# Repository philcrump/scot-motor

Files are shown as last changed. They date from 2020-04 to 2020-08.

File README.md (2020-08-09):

# scot-motor

Motor Interface for the SCOT.

* 9-36V DC Input
* STM32F042K6 Microcontroller @ 48MHz
* MCP2562 CAN 2.0A/B Communication Interface
* DRV8872 3.6A PWM H-Bridge Motor Driver
* INA260 Motor Voltage & Current Supply Monitoring
* NCV8450 800mA Clutch Driver
* E-Stop, End-of-travel Limit Interlocks support
  * Hardware CMOS NAND Logic (immune to software override)
  * Opto-isolation of Switches from Logic Inputs (power supply not isolated)

[**Circuit Board Schematic**](https://github.com/philcrump/scot-motor/raw/master/scot-motor-schematic.pdf)

## PCB (CAD Render)

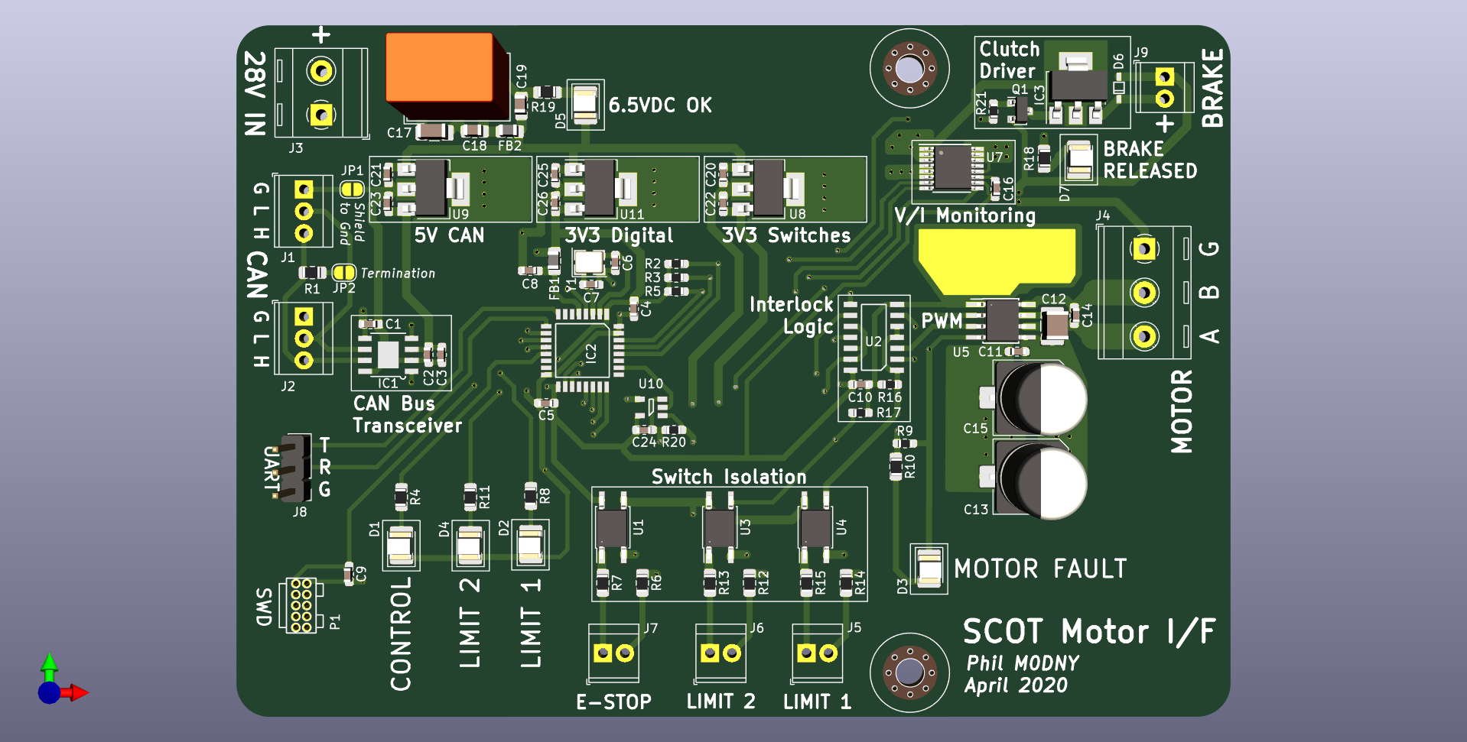
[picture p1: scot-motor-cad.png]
PCB CAD Render


### Errata - April 2020

* ~~0603 footprint used for C3 (4.7uF, 25V), should be 0805 - Minimal impact, 0805 still fits.~~ - Fixed in August 2020.

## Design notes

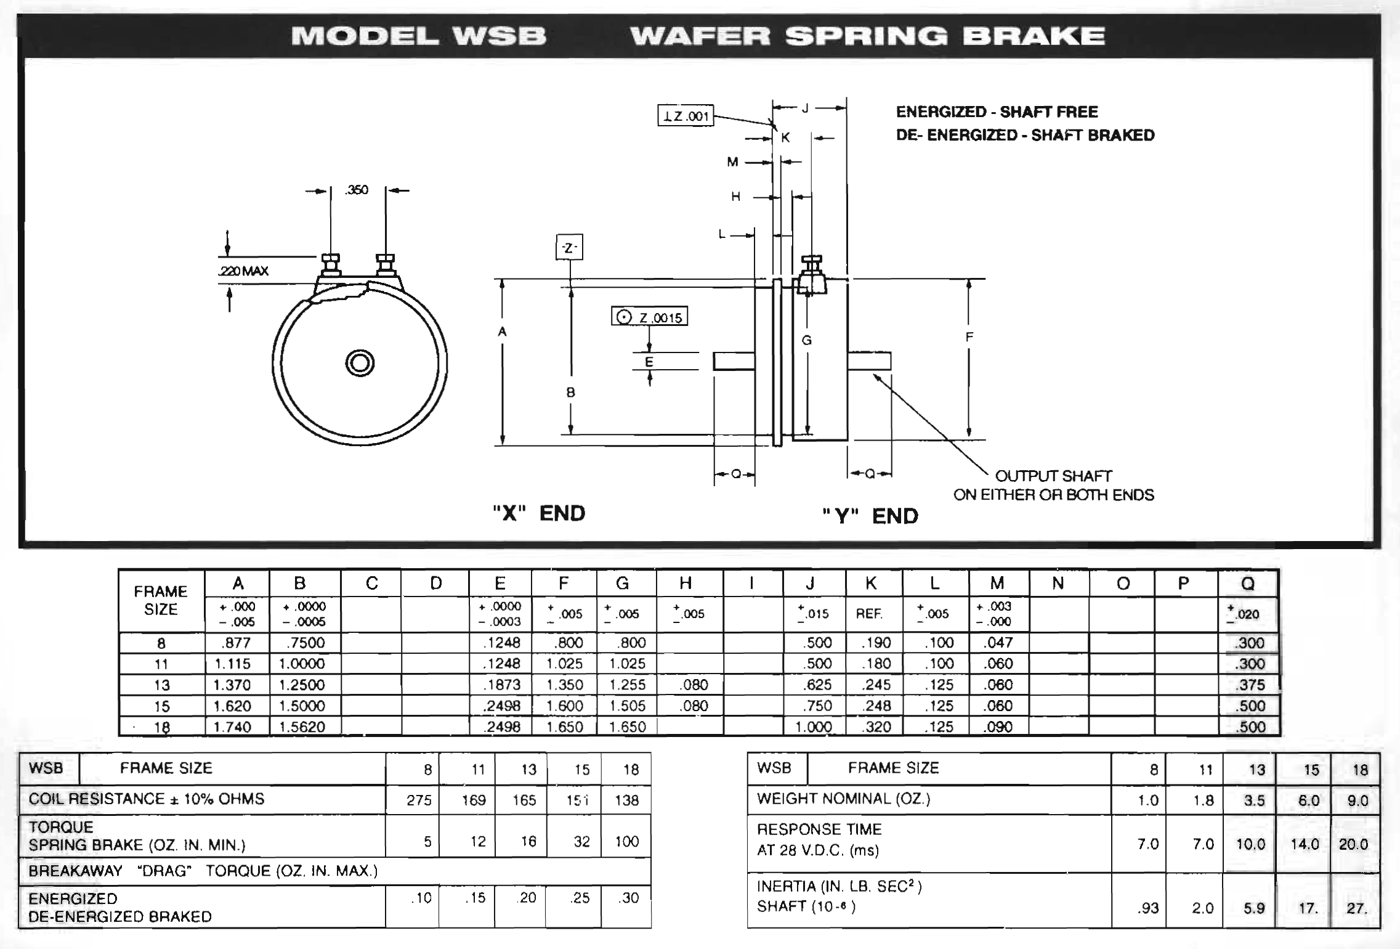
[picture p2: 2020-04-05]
datasheets/WSB_Brake.png

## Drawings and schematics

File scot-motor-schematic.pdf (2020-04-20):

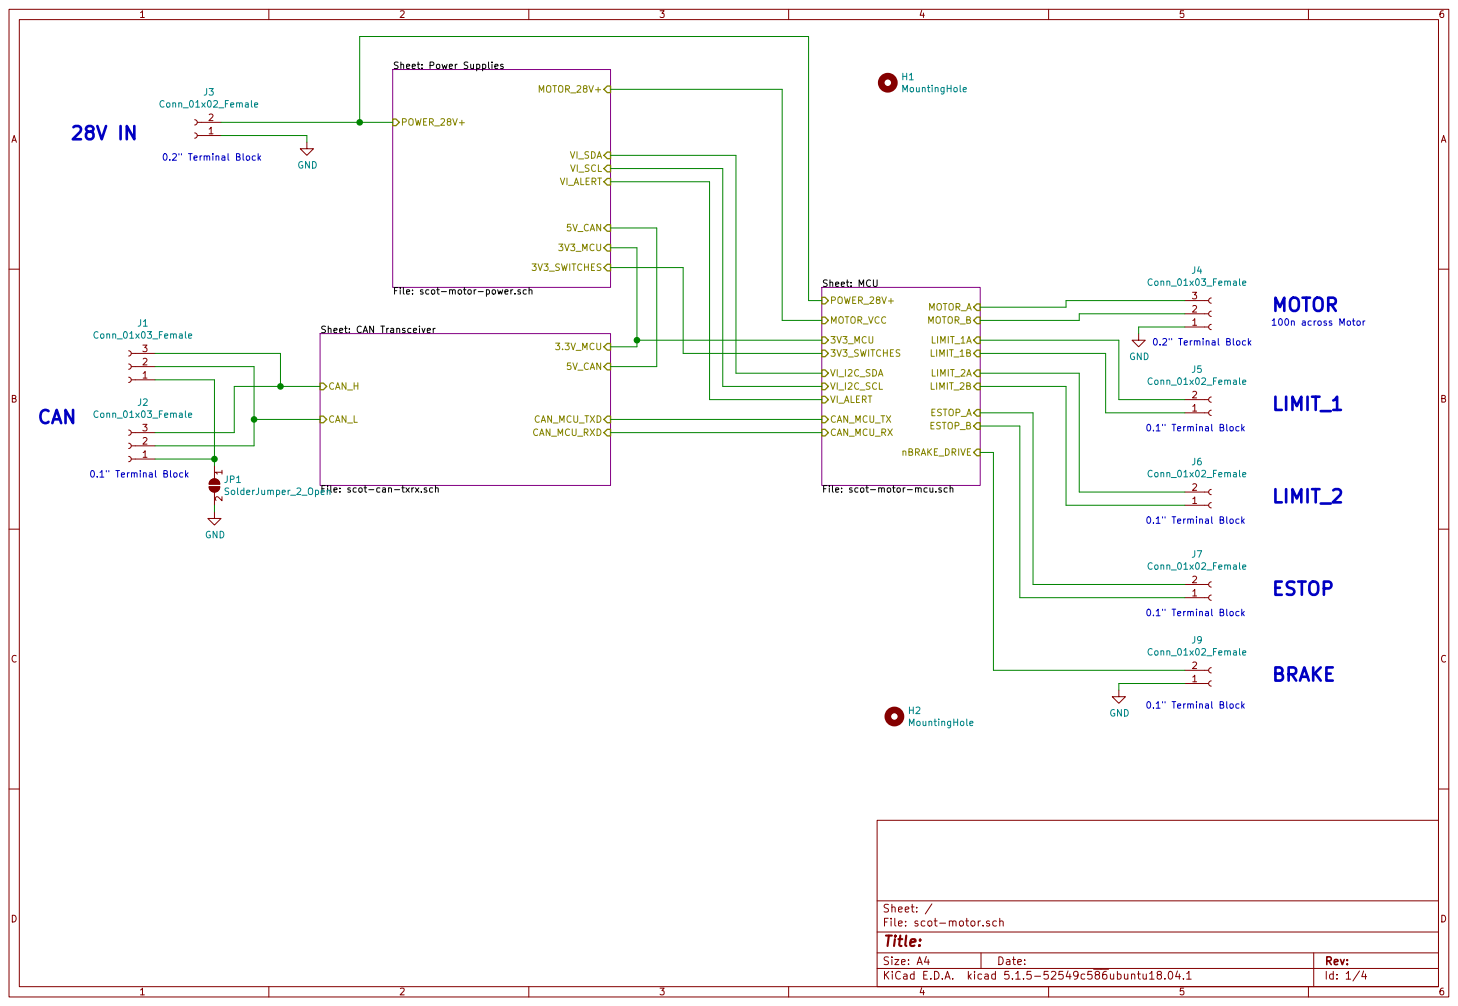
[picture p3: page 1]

File: scot-motor-power.sch POWER_28V+

Sheet: CAN Transceiver File: scot-can-txrx.sch CAN_L CAN_H

0.2" Terminal Block 0.1" Terminal Block 0.1" Terminal Block 0.1" Terminal Block CAN

Id: 1/4 Title: File: scot-motor.sch Sheet: /

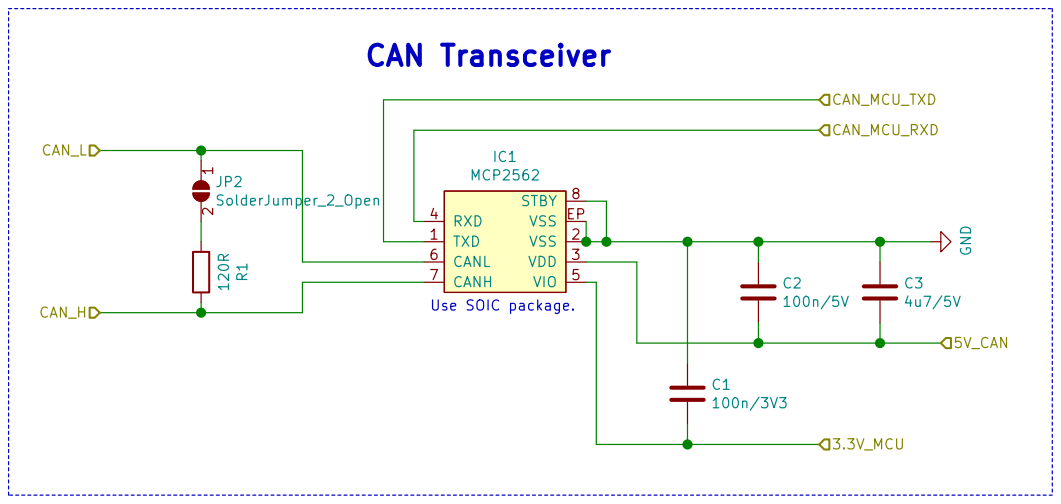
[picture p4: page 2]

Id: 2/4 Title: File: scot-can-txrx.sch Sheet: /CAN Transceiver/ R1 120R

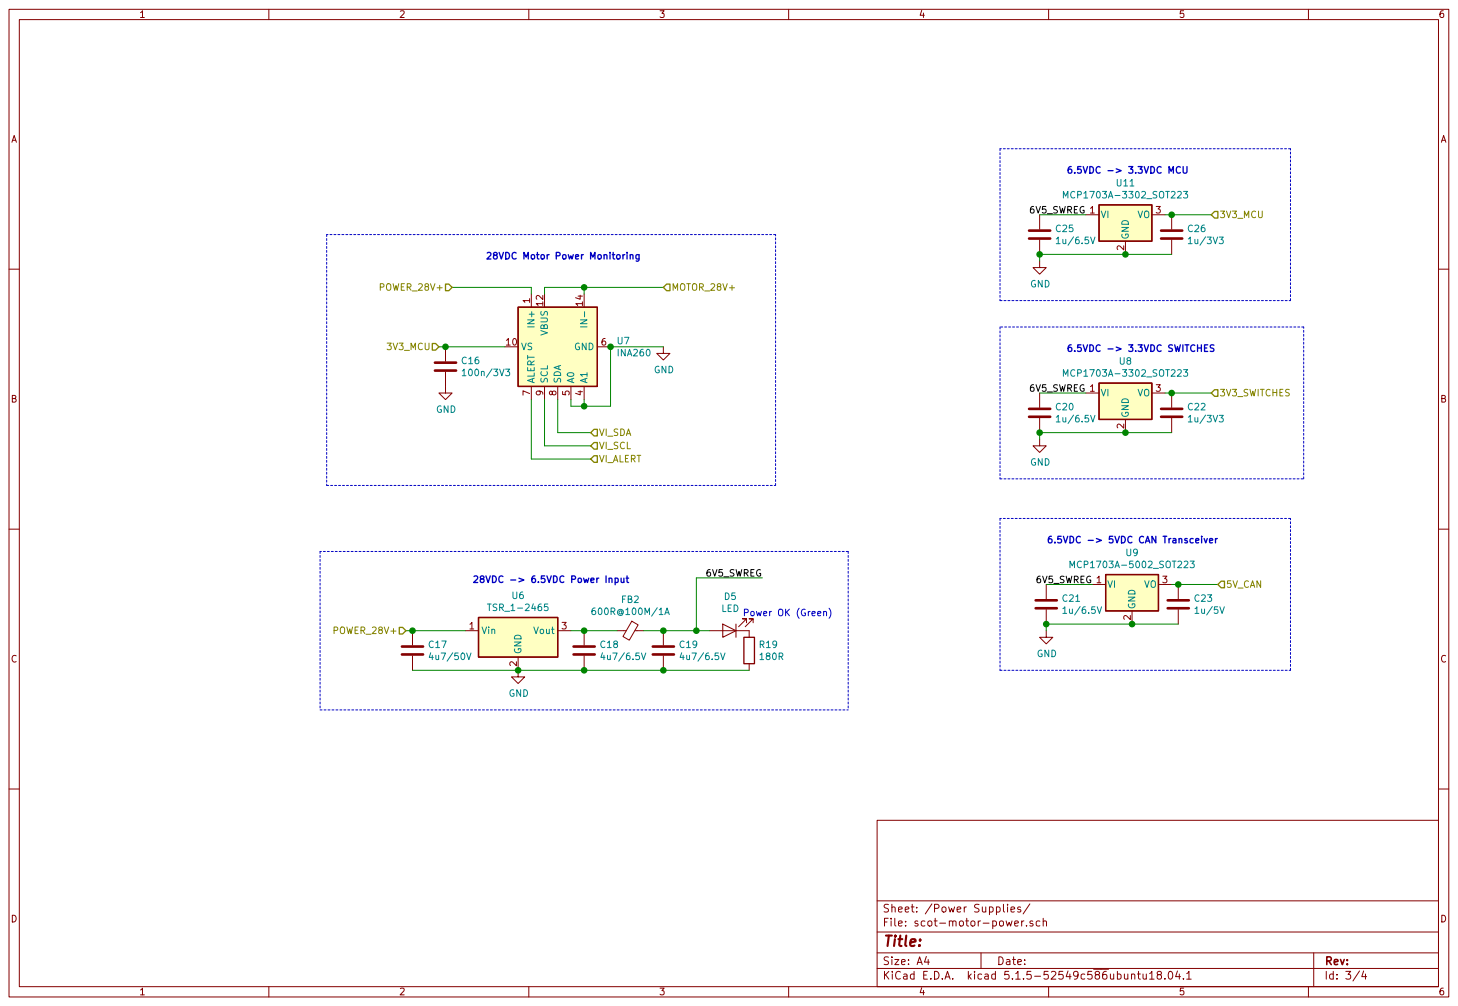
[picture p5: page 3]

Sheet: /Power Supplies/
File: scot-motor-power.sch
Id: 3/4 Title:

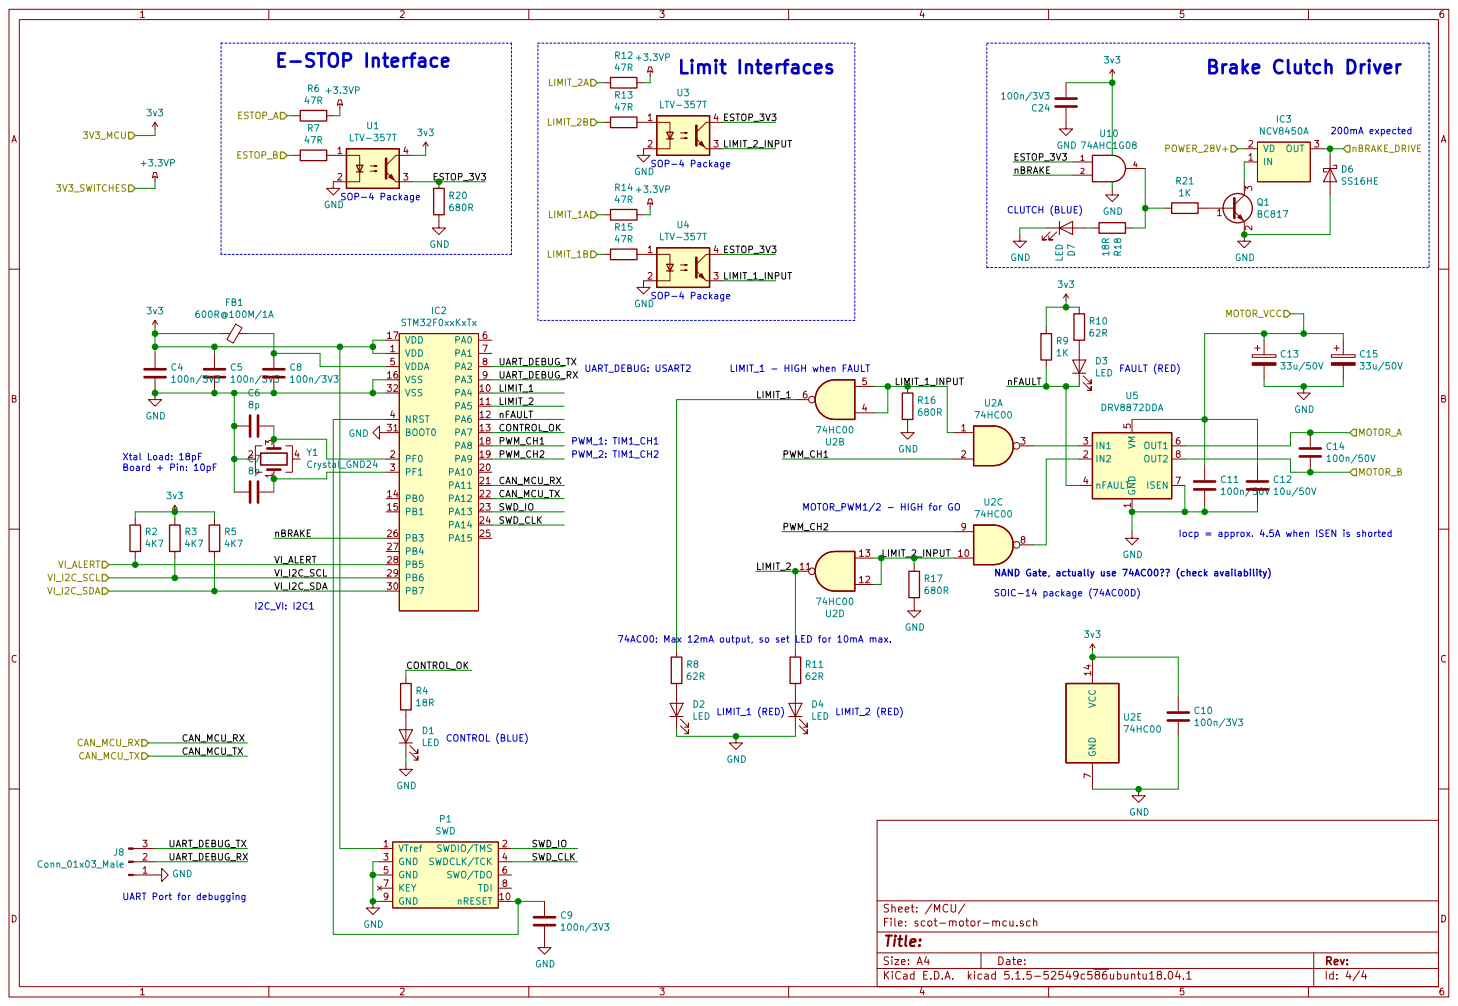
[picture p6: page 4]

CLUTCH (BLUE) MOTOR_PWM1/2 - HIGH for GO Limit Interfaces

Iocp = approx. 4.5A when ISEN is shorted

NAND Gate, actually use 74AC00?? (check availability)
SOIC-14 package (74AC00D)

74AC00: Max 12mA output, so set LED for 10mA max.

Id: 4/4 Title: File: scot-motor-mcu.sch Sheet: /MCU/ R8

UART Port for debugging

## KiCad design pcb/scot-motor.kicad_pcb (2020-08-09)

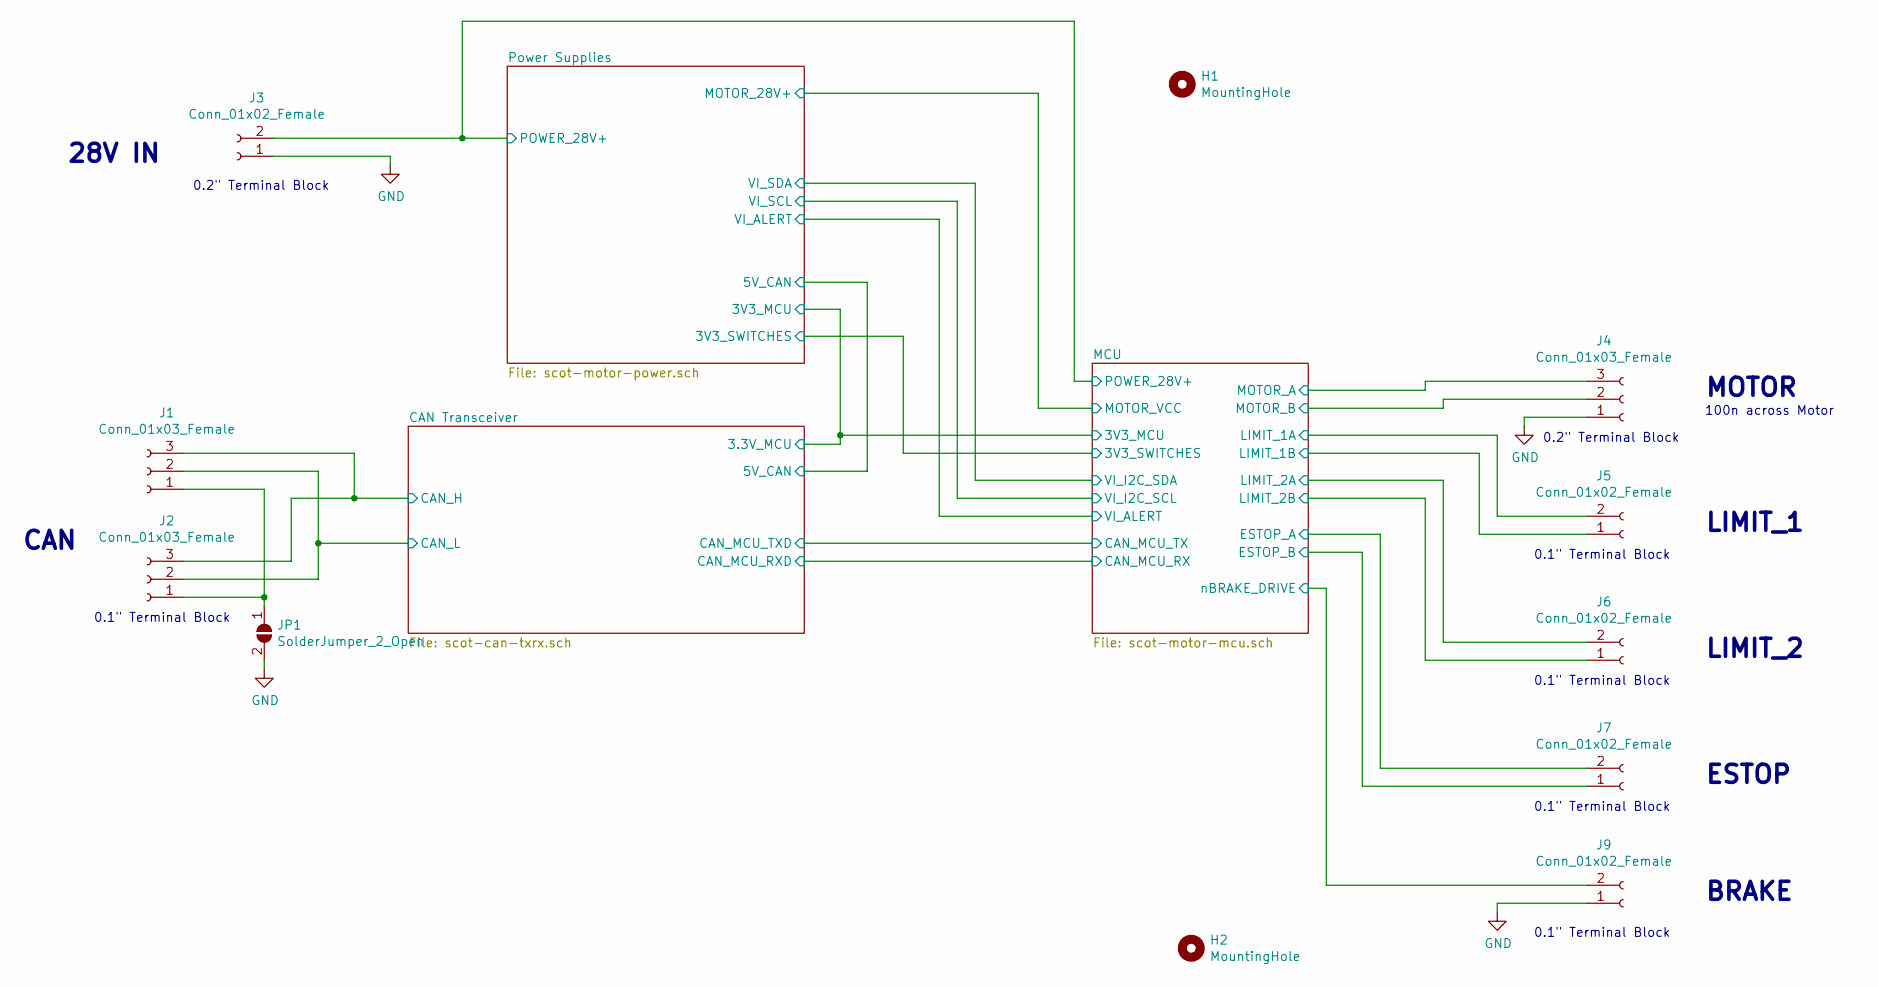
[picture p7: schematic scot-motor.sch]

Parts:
H1, H2: MountingHole; M3_MOUNT
J1, J2: Conn_01x03_Female; TerminalBlock_TE_282834-3_1x03_P2.54mm_Horizontal
J3: Conn_01x02_Female; TerminalBlock_RND_205-00287_1x02_P5.08mm_Horizontal
J4: Conn_01x03_Female; TerminalBlock_RND_205-00288_1x03_P5.08mm_Horizontal
J5, J6, J7, J9: Conn_01x02_Female; TerminalBlock_TE_282834-2_1x02_P2.54mm_Horizontal
JP1: SolderJumper_2_Open; SolderJumper-2_P1.3mm_Open_RoundedPad1.0x1.5mm

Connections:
/CAN Transceiver/CAN_H: J1.3, J2.3; also elsewhere on the board
/CAN Transceiver/CAN_L: J1.2, J2.2; also elsewhere on the board
/MCU/ESTOP_A: J7.2; also elsewhere on the board
/MCU/ESTOP_B: J7.1; also elsewhere on the board
/MCU/LIMIT_1A: J5.2; also elsewhere on the board
/MCU/LIMIT_1B: J5.1; also elsewhere on the board
/MCU/LIMIT_2A: J6.2; also elsewhere on the board
/MCU/LIMIT_2B: J6.1; also elsewhere on the board
/MCU/MOTOR_A: J4.3; also elsewhere on the board
/MCU/MOTOR_B: J4.2; also elsewhere on the board
/MCU/POWER_28V+: J3.2; also elsewhere on the board
/MCU/nBRAKE_DRIVE: J9.2; also elsewhere on the board
GND: J3.1, J4.1, J9.1, JP1.2 (B); also elsewhere on the board
unnamed: J1.1, J2.1, JP1.1 (A)

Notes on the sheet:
0.2" Terminal Block
0.1" Terminal Block
MOTOR
LIMIT_1
LIMIT_2
ESTOP
28V IN
CAN
100n across Motor
BRAKE

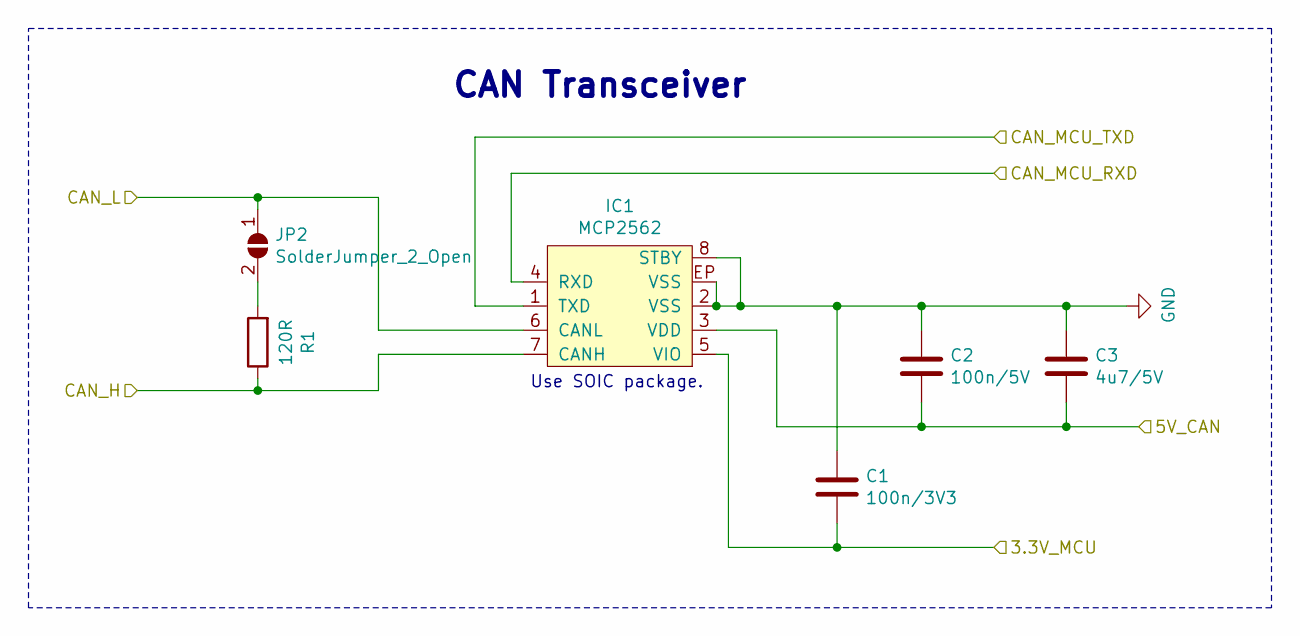
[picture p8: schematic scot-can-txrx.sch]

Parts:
C3: 4u7/5V; C_0805_2012Metric_Pad1.15x1.40mm_HandSolder
C53: 100n/3V3; C_0603_1608Metric_Pad1.05x0.95mm_HandSolder
C54: 100n/5V; C_0603_1608Metric_Pad1.05x0.95mm_HandSolder
IC1: MCP2562; SOIC-8-EP
JP2: SolderJumper_2_Open; SolderJumper-2_P1.3mm_Open_RoundedPad1.0x1.5mm
R36: 120R; R_0805_2012Metric_Pad1.15x1.40mm_HandSolder

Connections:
3v3: IC1.5 (VIO); also elsewhere on the board
/CAN Transceiver/5V_CAN: C3.2, IC1.3 (VDD); also elsewhere on the board
/CAN Transceiver/CAN_H: IC1.7 (CANH); also elsewhere on the board
/CAN Transceiver/CAN_L: IC1.6 (CANL), JP2.1 (A); also elsewhere on the board
/MCU/CAN_MCU_RX: IC1.4 (RXD); also elsewhere on the board
/MCU/CAN_MCU_TX: IC1.1 (TXD); also elsewhere on the board
GND: C3.1, IC1.2 (VSS), IC1.8 (STBY), IC1.EP (VSS); also elsewhere on the board
unnamed 57: JP2.2 (B); also elsewhere on the board

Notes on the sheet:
Use SOIC package.
CAN Transceiver

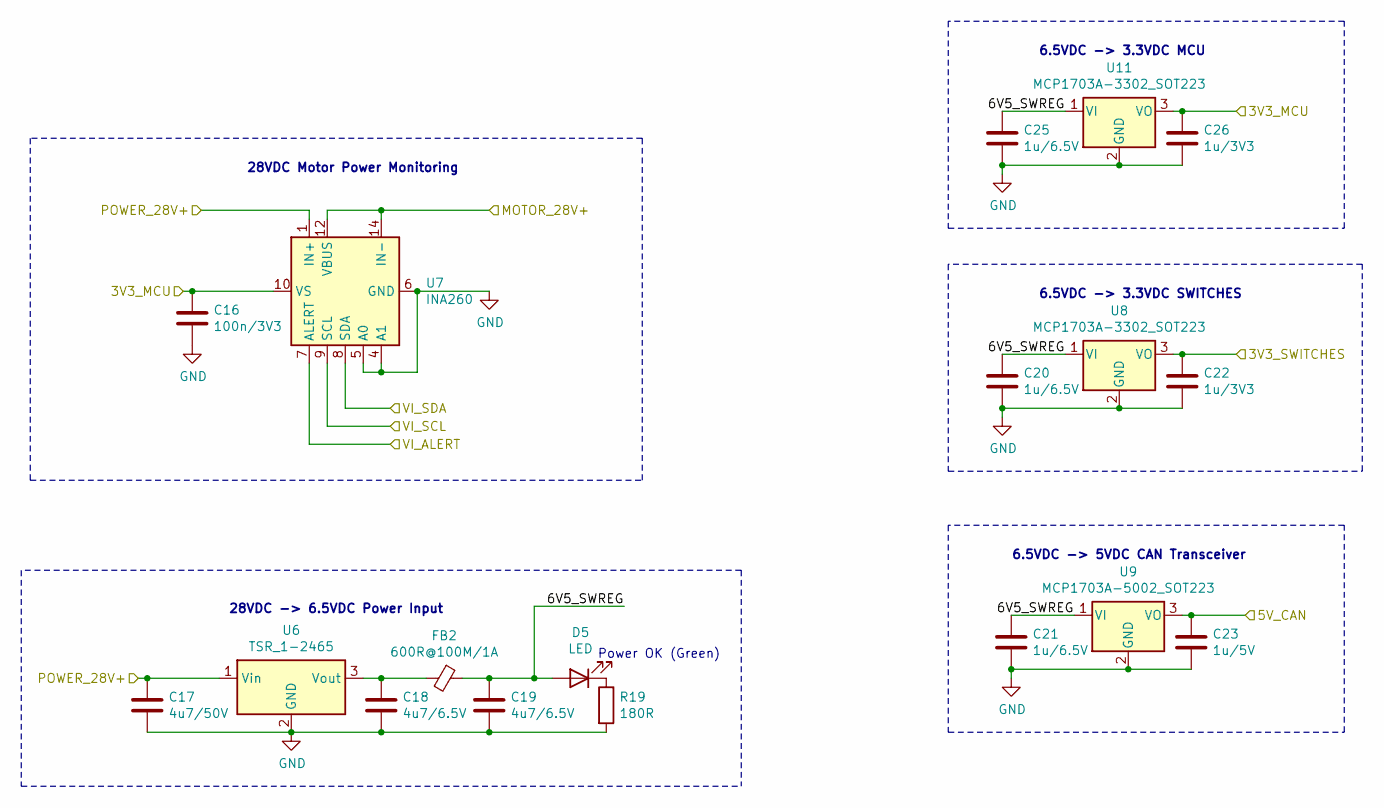
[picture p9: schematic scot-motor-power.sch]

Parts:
C16: 100n/3V3; C_0603_1608Metric_Pad1.05x0.95mm_HandSolder
C17: 4u7/50V; C_1206_3216Metric_Pad1.42x1.75mm_HandSolder
C18, C19: 4u7/6.5V; C_0805_2012Metric_Pad1.15x1.40mm_HandSolder
C20, C21, C25: 1u/6.5V; C_0603_1608Metric_Pad1.05x0.95mm_HandSolder
C22, C26: 1u/3V3; C_0603_1608Metric_Pad1.05x0.95mm_HandSolder
C23: 1u/5V; C_0603_1608Metric_Pad1.05x0.95mm_HandSolder
D5: LED; LED_1210_3225Metric_Pad1.42x2.65mm_HandSolder
FB2: 600R@100M/1A; L_0805_2012Metric_Pad1.15x1.40mm_HandSolder
R19: 180R; R_0805_2012Metric_Pad1.15x1.40mm_HandSolder
U6: TSR_1-2465; Converter_DCDC_TRACO_TSR-1_THT
U7: INA260; TSSOP-16_4.4x5mm_P0.65mm
U8, U11: MCP1703A-3302_SOT223; SOT-223-3_TabPin2
U9: MCP1703A-5002_SOT223; SOT-223-3_TabPin2

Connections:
3v3: C16.1, C26.1, U7.10 (VS), U11.3 (VO); also elsewhere on the board
+3.3VP: C22.1, U8.3 (VO); also elsewhere on the board
/CAN Transceiver/5V_CAN: C23.1, U9.3 (VO); also elsewhere on the board
/MCU/POWER_28V+: C17.1, U6.1 (Vin), U7.1 (IN+), U7.2 (IN+), U7.3 (IN+); also elsewhere on the board
/MCU/VI_ALERT: U7.7 (ALERT); also elsewhere on the board
/MCU/VI_I2C_SCL: U7.9 (SCL); also elsewhere on the board
/MCU/VI_I2C_SDA: U7.8 (SDA); also elsewhere on the board
/Power Supplies/6V5_SWREG: C19.1, C20.1, C21.1, C25.1, D5.2 (A), FB2.1, U8.1 (VI), U9.1 (VI), U11.1 (VI)
/Power Supplies/MOTOR_28V+: U7.12 (VBUS), U7.14 (IN-), U7.15 (IN-), U7.16 (IN-); also elsewhere on the board
GND: C16.2, C17.2, C18.2, C19.2, C20.2, C21.2, C22.2, C23.2, C25.2, C26.2, R19.2, U6.2 (GND), U7.4 (A1), U7.5 (A0), U7.6 (GND), U7.11 (GND), U8.2 (GND), U9.2 (GND), U11.2 (GND); also elsewhere on the board
unnamed: C18.1, FB2.2, U6.3 (Vout)
unnamed: D5.1 (K), R19.1

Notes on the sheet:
6.5VDC -> 5VDC CAN Transceiver
6.5VDC -> 3.3VDC SWITCHES
28VDC -> 6.5VDC Power Input
28VDC Motor Power Monitoring
Power OK (Green)
6.5VDC -> 3.3VDC MCU

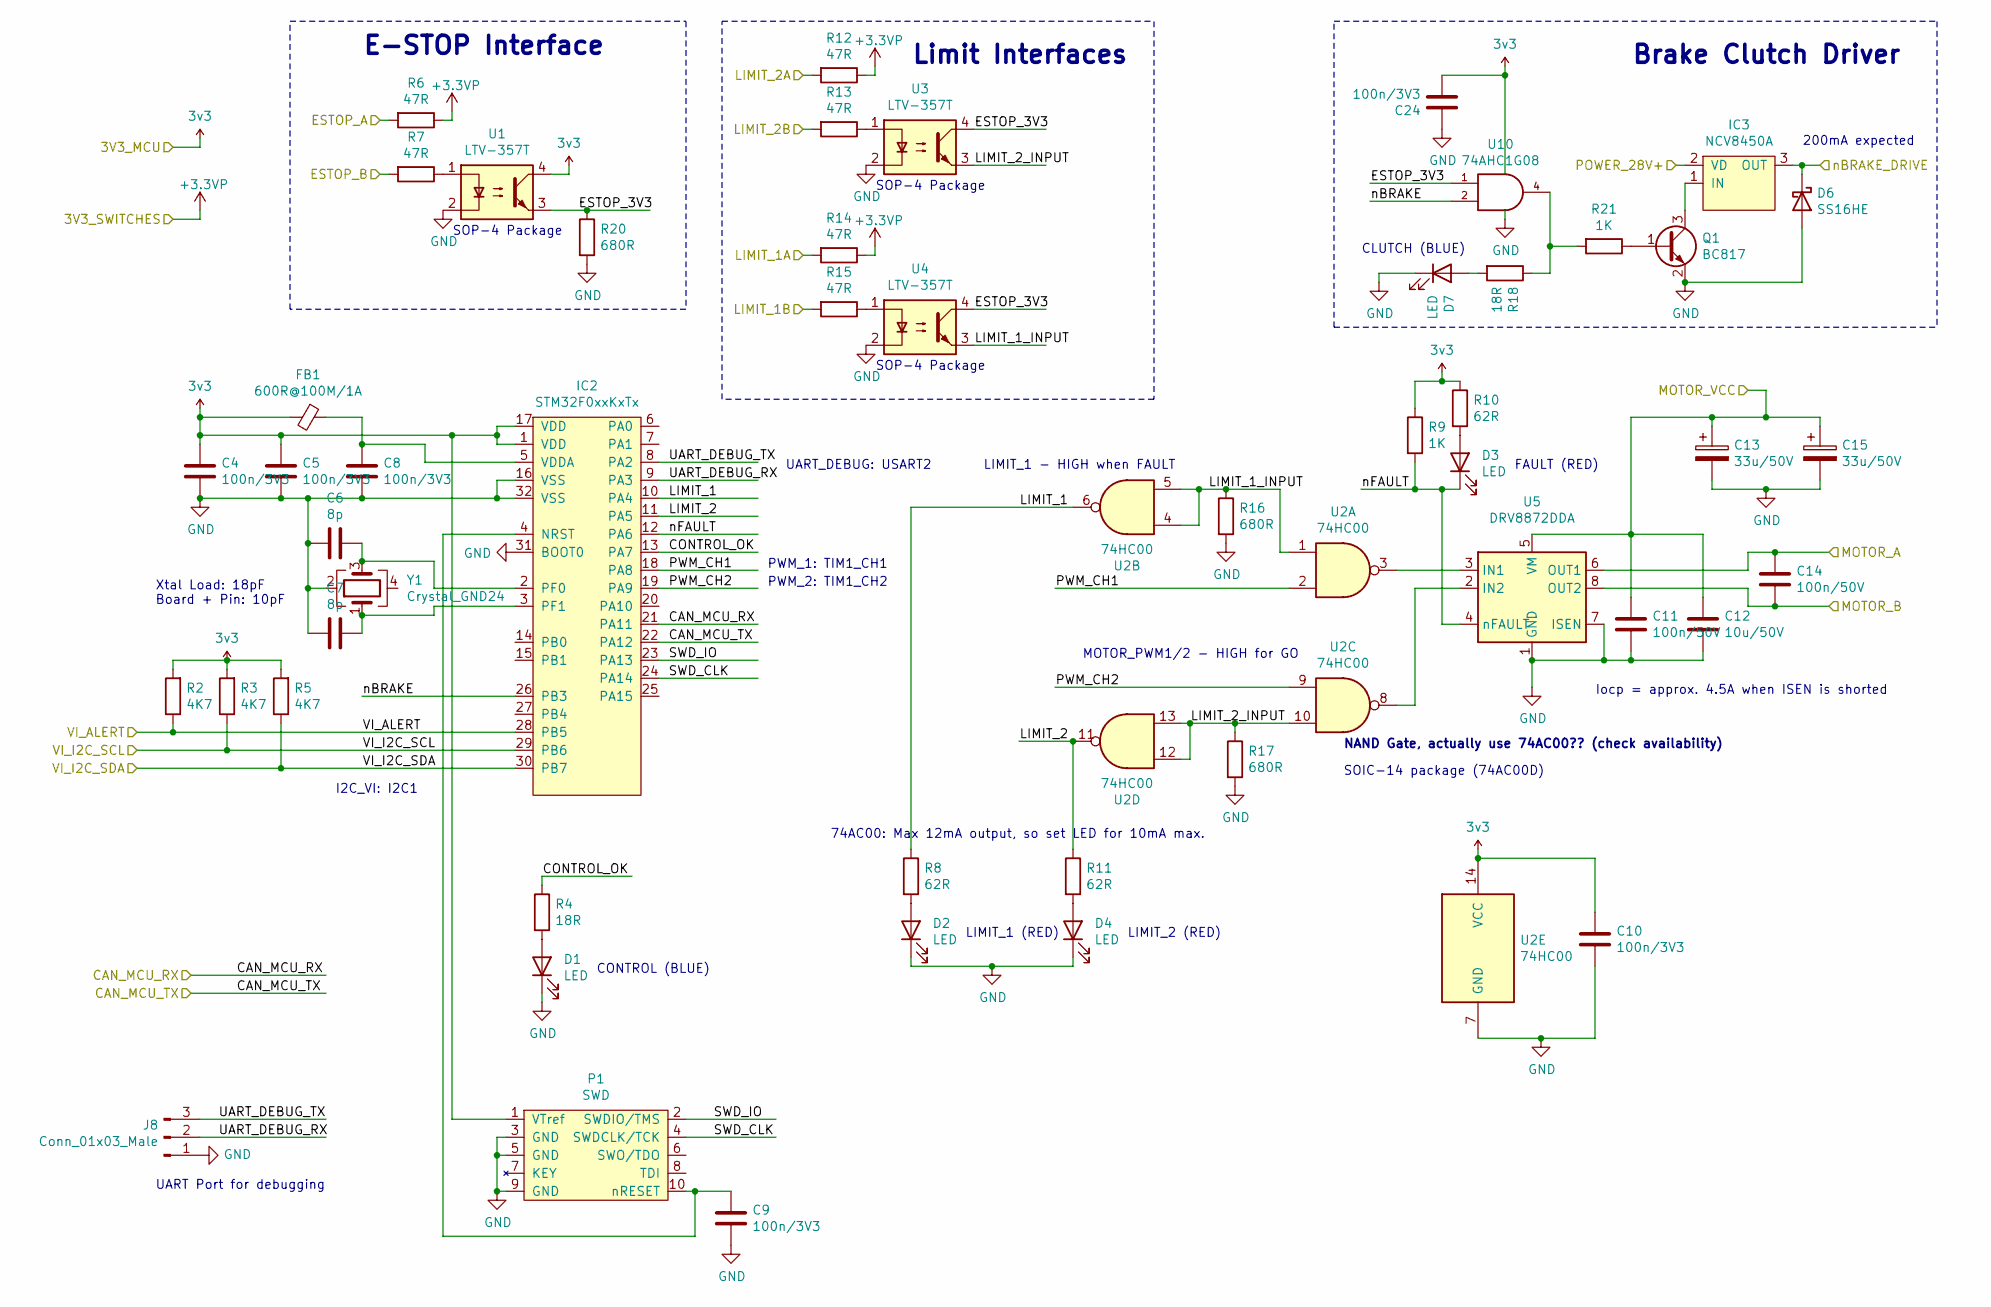
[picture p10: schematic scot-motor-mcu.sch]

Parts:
C4, C5, C8, C9, C10, C24: 100n/3V3; C_0603_1608Metric_Pad1.05x0.95mm_HandSolder
C6, C7: 8p; C_0603_1608Metric_Pad1.05x0.95mm_HandSolder
C11, C14: 100n/50V; C_0603_1608Metric_Pad1.05x0.95mm_HandSolder
C12: 10u/50V; C_1210_3225Metric_Pad1.42x2.65mm_HandSolder
C13, C15: 33u/50V; CP_Elec_8x10.5
D1, D2, D3, D4, D7: LED; LED_1210_3225Metric_Pad1.42x2.65mm_HandSolder
D6: SS16HE; SOD-323
FB1: 600R@100M/1A; L_0805_2012Metric_Pad1.15x1.40mm_HandSolder
IC2: STM32F0xxKxTx; LQFP-32; Farnell 2432085
IC3: NCV8450A; SOT-223-3_TabPin2; Mouser 863-NCV8450ASTT3G
J8: Conn_01x03_Male; PinHeader_1x03_P2.54mm_Vertical
P1: SWD; FTSH-105-01-F-D-K
Q1: BC817; SOT-23
R2, R3, R5: 4K7; R_0603_1608Metric_Pad1.05x0.95mm_HandSolder
R4, R18: 18R; R_0805_2012Metric_Pad1.15x1.40mm_HandSolder
R6, R7, R12, R13, R14, R15: 47R; R_0805_2012Metric_Pad1.15x1.40mm_HandSolder
R8, R10, R11: 62R; R_0805_2012Metric_Pad1.15x1.40mm_HandSolder
R9, R21: 1K; R_0603_1608Metric_Pad1.05x0.95mm_HandSolder
R16, R17, R20: 680R; R_0603_1608Metric_Pad1.05x0.95mm_HandSolder
U1, U3, U4: LTV-357T; SO-4_4.4x3.6mm_P2.54mm
U2: 74HC00; SOIC-14
U5: DRV8872DDA; Texas_HTSOP-8-1EP_3.9x4.9mm_P1.27mm_EP2.95x4.9mm_Mask2.4x3.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
U10: 74AHC1G08; SOT-23-5
Y1: Crystal_GND24; Crystal_SMD_Abracon_ABM8G-4Pin_3.2x2.5mm

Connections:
3v3: C4.1, C5.1, C10.1, C24.2, FB1.2, IC2.1 (VDD), IC2.17 (VDD), P1.1 (VTref), R2.2, R3.2, R5.2, R9.1, R10.1, U1.4, U2.14 (VCC), U10.5 (VCC); also elsewhere on the board
+3.3VP: R6.1, R12.1, R14.1; also elsewhere on the board
/MCU/CAN_MCU_RX: IC2.21 (PA11); also elsewhere on the board
/MCU/CAN_MCU_TX: IC2.22 (PA12); also elsewhere on the board
/MCU/CONTROL_OK: IC2.13 (PA7), R4.1
/MCU/ESTOP_3V3: R20.1, U1.3, U3.4, U4.4, U10.1
/MCU/ESTOP_A: R6.2; also elsewhere on the board
/MCU/ESTOP_B: R7.2; also elsewhere on the board
/MCU/LIMIT_1: IC2.10 (PA4), R8.1, U2.6
/MCU/LIMIT_1A: R14.2; also elsewhere on the board
/MCU/LIMIT_1B: R15.2; also elsewhere on the board
/MCU/LIMIT_1_INPUT: R16.1, U2.1, U2.4, U2.5, U4.3
/MCU/LIMIT_2: IC2.11 (PA5), R11.1, U2.11
/MCU/LIMIT_2A: R12.2; also elsewhere on the board
/MCU/LIMIT_2B: R13.2; also elsewhere on the board
/MCU/LIMIT_2_INPUT: R17.1, U2.10, U2.12, U2.13, U3.3
/MCU/MOTOR_A: C14.1, U5.6 (OUT1); also elsewhere on the board
/MCU/MOTOR_B: C14.2, U5.8 (OUT2); also elsewhere on the board
/MCU/POWER_28V+: IC3.2 (VD); also elsewhere on the board
/MCU/PWM_CH1: IC2.18 (PA8), U2.2
/MCU/PWM_CH2: IC2.19 (PA9), U2.9
/MCU/SWD_CLK: IC2.24 (PA14), P1.4 (SWDCLK/TCK)
/MCU/SWD_IO: IC2.23 (PA13), P1.2 (SWDIO/TMS)
/MCU/UART_DEBUG_RX: IC2.9 (PA3), J8.2
/MCU/UART_DEBUG_TX: IC2.8 (PA2), J8.3
/MCU/VI_ALERT: IC2.28 (PB5), R2.1; also elsewhere on the board
/MCU/VI_I2C_SCL: IC2.29 (PB6), R3.1; also elsewhere on the board
/MCU/VI_I2C_SDA: IC2.30 (PB7), R5.1; also elsewhere on the board
/MCU/nBRAKE: IC2.26 (PB3), U10.2
/MCU/nBRAKE_DRIVE: D6.1 (K), IC3.3 (OUT); also elsewhere on the board
/MCU/nFAULT: D3.1 (K), IC2.12 (PA6), R9.2, U5.4 (nFAULT)
/Power Supplies/MOTOR_28V+: C11.1, C12.1, C13.1, C15.1, U5.5 (VM); also elsewhere on the board
GND: C4.2, C5.2, C6.2, C7.2, C8.2, C9.2, C10.2, C11.2, C12.2, C13.2, C15.2, C24.1, D1.1 (K), D2.1 (K), D4.1 (K), D6.2 (A), D7.1 (K), IC2.16 (VSS), IC2.31 (BOOT0), IC2.32 (VSS), J8.1, P1.3 (GND), P1.5 (GND), P1.9 (GND), Q1.2 (E), R16.2, R17.2, R20.2, U1.2, U2.7 (GND), U3.2, U4.2, U5.1 (GND), U5.7 (ISEN), U5.9 (GND), U10.3 (GND), Y1.2; also elsewhere on the board
unnamed: C6.1, IC2.2 (PF0), Y1.3
unnamed: C7.1, IC2.3 (PF1), Y1.1
unnamed: C8.1, FB1.1, IC2.5 (VDDA)
unnamed: C9.1, IC2.4 (NRST), P1.10 (nRESET)
unnamed: D1.2 (A), R4.2
unnamed: D2.2 (A), R8.2
unnamed: D3.2 (A), R10.2
unnamed: D4.2 (A), R11.2
unnamed: D7.2 (A), R18.2
unnamed: IC3.1 (IN), Q1.3 (C)
unnamed: Q1.1 (B), R21.1
unnamed: R7.1, U1.1
unnamed: R13.1, U3.1
unnamed: R15.1, U4.1
unnamed: R18.1, R21.2, U10.4
unnamed: U2.3, U5.3 (IN1)
unnamed: U2.8, U5.2 (IN2)

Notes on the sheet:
Iocp = approx. 4.5A when ISEN is shorted
LIMIT_1 - HIGH when FAULT
MOTOR_PWM1/2 - HIGH for GO
NAND Gate, actually use 74AC00?? (check availability)
FAULT (RED)
LIMIT_2 (RED)
LIMIT_1 (RED)
UART Port for debugging
CONTROL (BLUE)
SOP-4 Package
I2C_VI: I2C1
UART_DEBUG: USART2
PWM_1: TIM1_CH1
PWM_2: TIM1_CH2
74AC00: Max 12mA output, so set LED for 10mA max.
SOIC-14 package (74AC00D)
200mA expected
E-STOP Interface
Brake Clutch Driver
Limit Interfaces
CLUTCH (BLUE)
Xtal Load: 18pF Board + Pin: 10pF

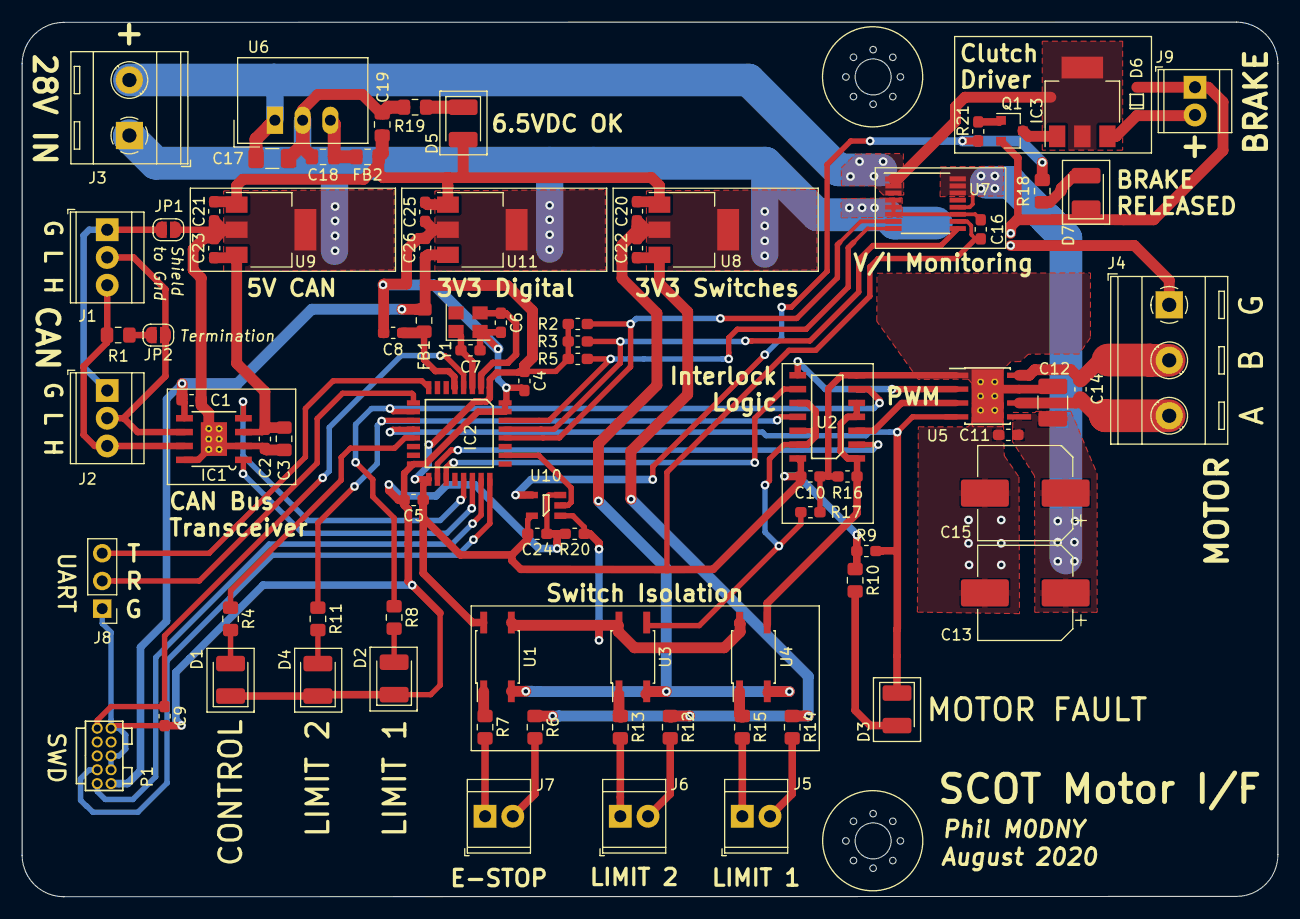
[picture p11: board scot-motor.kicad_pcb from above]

Board: 2 copper layers, 115.1 x 80.1 mm, 86 parts (0 on the bottom side), 58 nets.

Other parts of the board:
C1: 100n/3V3; C_0603_1608Metric_Pad1.05x0.95mm_HandSolder
C2: 100n/5V; C_0603_1608Metric_Pad1.05x0.95mm_HandSolder
R1: 120R; R_0805_2012Metric_Pad1.15x1.40mm_HandSolder

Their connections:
3v3: C1.2; also elsewhere on the board
/CAN Transceiver/5V_CAN: C2.2; also elsewhere on the board
/CAN Transceiver/CAN_H: R1.1; also elsewhere on the board
GND: C1.1, C2.1; also elsewhere on the board
unnamed 57: R1.2; also elsewhere on the board

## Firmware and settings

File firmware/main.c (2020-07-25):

#include "main.h"
#include "chprintf.h"

extern char config_device_id_hexstr[25];
extern char config_can_address_prefix_hexstr[5];

static const SerialConfig serial_cfg = {
  115200,
  0,
  0,
  0
};

void sdWriteString(SerialDriver *sdp, const char *string)
{
  uint32_t i;
  for(i = 0; string[i] != '\0'; i++)
  {
    sdPut(sdp, string[i]);
  }
}

THD_WORKING_AREA(can_rx_service_wa, 128);
THD_WORKING_AREA(watchdog_service_wa, 128);
THD_WORKING_AREA(diagnostics_service_wa, 128);

int main(void)
{
  halInit();
  chSysInit();

  watchdog_init();
  chThdCreateStatic(watchdog_service_wa, sizeof(watchdog_service_wa), HIGHPRIO, watchdog_service_thread, NULL);

  config_init();

  /* Start Debug Console */
  sdStart(&SD2, &serial_cfg);

  sdWriteString(&SD2, "SCOT Motor Interface - Phil Crump M0DNY\r\n");
  sdWriteString(&SD2, " - Version: " GITVERSION "\r\n");
  sdWriteString(&SD2, " - STM32 ID: ");
  sdWriteString(&SD2, config_device_id_hexstr);
  sdWriteString(&SD2, "\r\n");
  sdWriteString(&SD2, " - CAN ADDRESS: ");
  sdWriteString(&SD2, config_can_address_prefix_hexstr);
  sdWriteString(&SD2, "\r\n");

  if(!vi_init())
  {
    sdWriteString(&SD2, "VI Init FAILED\r\n");
    system_reset();
  }

  signals_init();
  motor_init();

  chThdCreateStatic(can_rx_service_wa, sizeof(can_rx_service_wa), NORMALPRIO, can_rx_service_thread, NULL);

  chThdCreateStatic(diagnostics_service_wa, sizeof(diagnostics_service_wa), NORMALPRIO, diagnostics_service_thread, NULL);

  while(true)
  {
    chThdSleepMilliseconds(100);
    watchdog_feed(WATCHDOG_DOG_MAIN);
  }
}

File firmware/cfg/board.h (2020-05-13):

/*
    ChibiOS - Copyright (C) 2006..2018 Giovanni Di Sirio

    Licensed under the Apache License, Version 2.0 (the "License");
    you may not use this file except in compliance with the License.
    You may obtain a copy of the License at

        http://www.apache.org/licenses/LICENSE-2.0

    Unless required by applicable law or agreed to in writing, software
    distributed under the License is distributed on an "AS IS" BASIS,
    WITHOUT WARRANTIES OR CONDITIONS OF ANY KIND, either express or implied.
    See the License for the specific language governing permissions and
    limitations under the License.
*/

#ifndef BOARD_H
#define BOARD_H

/*===========================================================================*/
/* Driver constants.                                                         */
/*===========================================================================*/

/*
 * Setup for Phil Crump's SCOT Resolver Interface board.
 */

/*
 * Board identifier.
 */
#define BOARD_SCOT_RESOLVER_rFeb2020
#define BOARD_NAME                  "SCOT Resolver Interface - Feb 2020"

/*
 * Board oscillators-related settings.
 * NOTE: LSE not fitted.
 * NOTE: HSE 8MHz 10ppm XTAL fitted.
 */
#if !defined(STM32_LSECLK)
#define STM32_LSECLK                0U
#endif

#define STM32_LSEDRV                (3U << 3U)

#if !defined(STM32_HSECLK)
#define STM32_HSECLK                8000000U
#endif

/*
 * MCU type as defined in the ST header.
 */
#define STM32F042x6

/*
 * IO pins assignments.
 */
#define GPIOA_PIN0                  0U
#define GPIOA_PIN1                  1U
#define GPIOA_UART_TX               2U
#define GPIOA_UART_RX               3U
#define GPIOA_LIMIT_1               4U
#define GPIOA_LIMIT_2               5U
#define GPIOA_PWM_nFAULT            6U
#define GPIOA_CONTROL_OK            7U
#define GPIOA_PWM_CH1               8U
#define GPIOA_PWM_CH2               9U
#define GPIOA_PIN10                 10U
#define GPIOA_CAN_RX                11U
#define GPIOA_CAN_TX                12U
#define GPIOA_SWDIO                 13U
#define GPIOA_SWCLK                 14U
#define GPIOA_PIN15                 15U

#define GPIOB_PIN0                  0U
#define GPIOB_PIN1                  1U
//#define GPIOB_PIN2                  2U
#define GPIOB_nBRAKE                3U
#define GPIOB_PIN4                  4U
#define GPIOB_VI_ALERT              5U
#define GPIOB_VI_SCL                6U
#define GPIOB_VI_SDA                7U
#define GPIOB_BOOT0                 8U

#define GPIOF_OSC_IN                0U
#define GPIOF_OSC_OUT               1U

/*
 * IO lines assignments.
 */
#define LINE_LIMIT_1                PAL_LINE(GPIOA, GPIOA_LIMIT_1)
#define LINE_LIMIT_2                PAL_LINE(GPIOA, GPIOA_LIMIT_2)
#define LINE_PWM_nFAULT             PAL_LINE(GPIOA, GPIOA_PWM_nFAULT)
#define LINE_CONTROL_OK             PAL_LINE(GPIOA, GPIOA_CONTROL_OK)

#define LINE_nBRAKE                 PAL_LINE(GPIOB, GPIOB_nBRAKE)
#define LINE_VI_ALERT               PAL_LINE(GPIOB, GPIOB_VI_ALERT)

/*===========================================================================*/
/* Driver pre-compile time settings.                                         */
/*===========================================================================*/

/*===========================================================================*/
/* Derived constants and error checks.                                       */
/*===========================================================================*/

/*===========================================================================*/
/* Driver data structures and types.                                         */
/*===========================================================================*/

/*===========================================================================*/
/* Driver macros.                                                            */
/*===========================================================================*/
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

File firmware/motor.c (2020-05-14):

#include "main.h"

static PWMConfig pwmcfg = {
  1024*20000,                               /* 20kHz PWM clock frequency     */
  1024,                                     /* Initial PWM period 1 second   */
  NULL,                                     /* No period callback            */
  {
   {PWM_OUTPUT_ACTIVE_HIGH, NULL},          /* CH1: Active High, no callback */
   {PWM_OUTPUT_ACTIVE_HIGH, NULL},          /* CH2: Active High, no callback */
   {PWM_OUTPUT_DISABLED, NULL},             /* CH3: Disabled                 */
   {PWM_OUTPUT_DISABLED, NULL}              /* CH4: Disabled                 */
  },
  0,                                        /* Control Register 2.            */
  0                                         /* DMA/Interrupt Enable Register. */
};

static uint16_t motor_speed_commanded = 0;

void motor_init(void)
{
    pwmStart(&PWMD1, &pwmcfg);
    motor_set_stop();
}

static inline void motor_set_stop_ch0(void)
{
  if(pwmIsChannelEnabledI(&PWMD1, 0))
  {
    pwmDisableChannel(&PWMD1, 0);
  }
}

static inline void motor_set_stop_ch1(void)
{
  if(pwmIsChannelEnabledI(&PWMD1, 1))
  {
    pwmDisableChannel(&PWMD1, 1);
  }
}


void motor_set_stop(void)
{
  motor_set_stop_ch0();
  motor_set_stop_ch1();

  brake_set_engaged();

  motor_speed_commanded = 0;
}

void motor_set_speed(int16_t speed)
{
  if(!control_timer_get_motor_enable())
  {
    motor_set_stop();
    return;
  }

  if(speed == 0)
  {
    motor_set_stop();
  }
  else
  {
    brake_set_released();

    if(speed > 0)
    {
      motor_set_stop_ch1();
      if(speed > 1024)
      {
        speed = 1024;
      }
      pwmEnableChannel(&PWMD1, 0, (uint32_t)speed);
      motor_speed_commanded = speed;
    }
    else
    {
      motor_set_stop_ch0();
      if(speed < -1024)
      {
        speed = -1024;
      }
      pwmEnableChannel(&PWMD1, 1, (uint32_t)(-1*speed));
      motor_speed_commanded = speed;
    }
  } 
}

int16_t motor_get_speed_commanded(void)
{
  return motor_speed_commanded;
}

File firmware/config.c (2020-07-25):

#include "main.h"

#include <string.h>

#define STM32_ID_ADDR 0x1FFFF7AC

uint8_t config_device_id[12];
char config_device_id_hexstr[25];

uint32_t config_can_address_prefix = 0x0000;
char config_can_address_prefix_hexstr[5];

/* CAN Address is 0x7ff

Location:
  0x1__ : Azimuth
  0x2__ : Elevation
  0x3__ : Base

Function:
  0x_1_ : Resolver
  0x_2_ : Motor
  0x_3_ : Controller
*/

#define CAN_ADDRESS_PREFIX_ELEVATION  0x100
#define CAN_ADDRESS_PREFIX_AZIMUTH    0x200
#define CAN_ADDRESS_PREFIX_BASE       0x300

#define CAN_ADDRESS_PREFIX_RESOLVER   0x010
#define CAN_ADDRESS_PREFIX_MOTOR      0x020
#define CAN_ADDRESS_PREFIX_CONTROLLER 0x030

static const uint8_t config_device_id_el_motor[12] = { 0x0F, 0x00, 0x22, 0x00, 0x0B, 0x43, 0x4E, 0x57, 0x37, 0x39, 0x35, 0x20 };
static const uint8_t config_device_id_az_motor[12] = { 0x01, 0x80, 0x02, 0x00, 0x13, 0x43, 0x4E, 0x47, 0x33, 0x38, 0x32, 0x20 };

#define CONFIG_MATCH_DEVICE_ID(a,b) (memcmp((void *)a,(void *)b,12)==0)

void config_init(void)
{
  /* Load STM32 96-bit device ID from ROM */
  config_device_id[0] = (uint8_t)((uint8_t *)STM32_ID_ADDR)[0];
  config_device_id[1] = (uint8_t)((uint8_t *)STM32_ID_ADDR)[1];
  config_device_id[2] = (uint8_t)((uint8_t *)STM32_ID_ADDR)[2];
  config_device_id[3] = (uint8_t)((uint8_t *)STM32_ID_ADDR)[3];
  config_device_id[4] = (uint8_t)((uint8_t *)STM32_ID_ADDR)[4];
  config_device_id[5] = (uint8_t)((uint8_t *)STM32_ID_ADDR)[5];
  config_device_id[6] = (uint8_t)((uint8_t *)STM32_ID_ADDR)[6];
  config_device_id[7] = (uint8_t)((uint8_t *)STM32_ID_ADDR)[7];
  config_device_id[8] = (uint8_t)((uint8_t *)STM32_ID_ADDR)[8];
  config_device_id[9] = (uint8_t)((uint8_t *)STM32_ID_ADDR)[9];
  config_device_id[10] = (uint8_t)((uint8_t *)STM32_ID_ADDR)[10];
  config_device_id[11] = (uint8_t)((uint8_t *)STM32_ID_ADDR)[11];

  /* Convert to hex for display */
  int32_t i;
  uint32_t remainder;

  for(i = 0; i < 12; i++)
  {
    remainder = config_device_id[i] & 0xF;
    if(remainder < 10)
    {
      config_device_id_hexstr[(i*2)+1] = 48 + remainder;
    }
    else
    {
      config_device_id_hexstr[(i*2)+1] = 55 + remainder;
    }

    remainder = config_device_id[i] >> 4;
    if(remainder < 10)
    {
      config_device_id_hexstr[i*2] = 48 + remainder;
    }
    else
    {
      config_device_id_hexstr[i*2] = 55 + remainder;
    }
  }
  config_device_id_hexstr[24] = '\0';

  /* Look up corresponding CAN address */
  config_can_address_prefix = 0x0000;
  if(CONFIG_MATCH_DEVICE_ID(config_device_id, config_device_id_el_motor))
  {
    /*
      "SCOT Motor I/F" - April 2020
      Clutch Driver & Limit switch ports fitted.
    */
    config_can_address_prefix |= CAN_ADDRESS_PREFIX_ELEVATION;
    config_can_address_prefix |= CAN_ADDRESS_PREFIX_MOTOR;
  }
  else if(CONFIG_MATCH_DEVICE_ID(config_device_id, config_device_id_az_motor))
  {
    /*
      "SCOT Motor I/F" - April 2020
      No clutch driver or limit switch port fitted
    */
    config_can_address_prefix |= CAN_ADDRESS_PREFIX_AZIMUTH;
    config_can_address_prefix |= CAN_ADDRESS_PREFIX_MOTOR;
  }

  /* Convert CAN address to hex for display */
  uint16_t quotient = config_can_address_prefix;
  for(i = 3; i >= 0; i--)
  {
    remainder = quotient & 0x7;

    if(remainder < 10)
    {
      config_can_address_prefix_hexstr[i] = 48 + remainder;
    }
    else
    {
      config_can_address_prefix_hexstr[i] = 55 + remainder;
    }

    quotient = quotient >> 4;
  }
  config_can_address_prefix_hexstr[4] = '\0';
}

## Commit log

2020-02-25 Initial commit.
    [scot-can-txrx.sch, scot-motor-driver.sch, scot-motor-limits.sch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]
2020-04-05 Add schematic.
2020-04-05 pcb: Add brake clutch driver.
    [scot-motor-mcu.sch, scot-motor-power.sch, scot-motor.kicad_pcb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]
2020-04-06 pcb: Link brake clutch to e-stop, aesthetic tweaks.
    [scot-can-txrx.sch, scot-motor-mcu.sch, scot-motor-power.sch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]
2020-04-11 PCB progress, schematic fixes.
    [scot-motor-mcu.sch, scot-motor-power.sch, scot-motor.kicad_pcb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]
2020-04-16 PCB progress.
    [scot-motor-mcu.sch, scot-motor-power.sch, scot-motor.kicad_pcb]
2020-04-18 pcb: Add ground terminal on motor terminal block for shielding.
    [scot-motor.kicad_pcb, scot-motor.sch]
2020-04-18 pcb: Add Clutch Release indicator.
    [scot-motor-mcu.sch, scot-motor.kicad_pcb]
2020-04-18 pcb: Final tweaks.
    [scot-motor-power.sch, scot-motor.kicad_pcb]
2020-04-18 pcb: Fix some DRC warnings, produce gerbers for cam.
    [scot-motor-B_Cu.gbr, scot-motor-B_Mask.gbr, scot-motor-B_Paste.gbr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]
2020-04-19 pcb: Add BOM list. Adjust some values to reduce lines.
    [scot-can-txrx.sch, scot-motor-mcu.sch, scot-motor-power.sch]
2020-04-20 pcb: Fix MCU xtal load capacitors.
    [scot-motor-mcu.sch]
2020-06-05 pcb/BOM: Use same 100n as other projects.
2020-07-25 firmware/: Load CAN addresses from STM32 ID lookup, add both board STM32 IDs.
2020-08-09 pcb/: Fixi C3 footprint and re-plot.
    [scot-can-txrx.sch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]
